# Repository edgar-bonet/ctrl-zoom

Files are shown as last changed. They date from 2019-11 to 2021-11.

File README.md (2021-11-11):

# LANC zoom controller

This project is a circuit board intended to control a DC motor from a
“zoom controller” wired remote conforming to the Sony's LANC protocol.

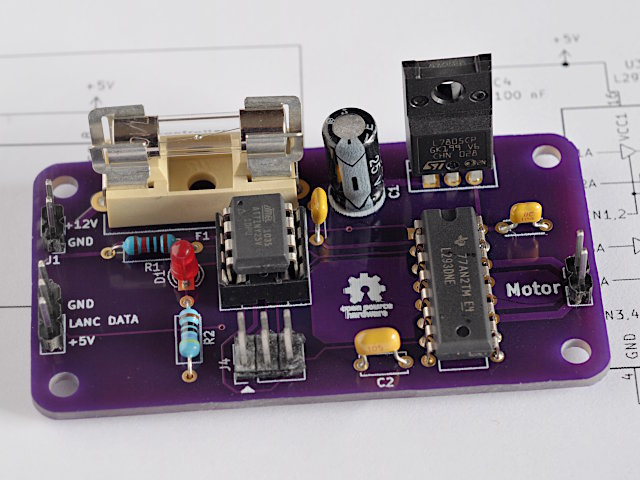
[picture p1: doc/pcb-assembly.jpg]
PCB assembly


## Motivation

Many people use DSLRs to record high-quality video despite their
inferior ergonomics relative to conventional camcorders. When mounted on
a tripod, many camcorders can be zoomed in and out using a wired remote
control, commonly known as a “[zoom controller][]”. In contrast, most
DSLRs have non-motorized zooms, and reaching for the zoom ring is
inconvenient when the camera is tripod-mounted.

The purpose of this project is to be able to control the zoom ring of a
DSLR using the same kind of wired remote one would use with a camcorder.
Specifically, this circuit board interfaces with remotes supporting the
widely used Sony's [LANC protocol][], and is capable of driving a
low-power DC motor from a 12&nbsp;V power supply. It is up to the user
to rig a DC motor to the zoom ring of their lens.

[zoom controller]: http://www.google.com/search?q=LANC+zoom+controller
[LANC protocol]: https://en.wikipedia.org/wiki/LANC

## Principle of operation

The main parts of the circuit are an [H bridge][] for driving the DC
motor and an [ATtiny][] microcontroller for driving the H bridge and
handling the communication with the wired remote.

The remote sends commands such as “zoom in at speed #2” or “zoom out at
speed #5”. In response to these commands, the microcontroller sets the
direction of rotation of the motor, and sends a [PWM][] signal to the
“enable” input of the H bridge. The duty cycle of the PWM signal depends
on the speed selected by the remote. This duty cycle in turn controls
the average power received by the DC motor. There is no feedback from
the motor, thus no precise control on its actual rotational speed.

[H bridge]: https://en.wikipedia.org/wiki/H_bridge
[ATtiny]: https://www.microchip.com/wwwproducts/en/ATtiny25
[PWM]: https://en.wikipedia.org/wiki/Pulse-width_modulation

## Building the circuit

Build the PCB according to the layout file
[ctrl-zoom.kicad\_pcb](board/ctrl-zoom.kicad_pcb), which is in the
format of the free [KiCad design software][KiCad]. Many professional PCB
shops can do it for you if you provide the proper design files. Some
accept the KiCad format directly, and need only that file. Others
require the design to be provided as a set of “Gerber” and drill files.
In this case, [install KiCad][KiCad-download], open ctrl-zoom.kicad\_pcb
with KiCad, and let it generate the required files (menu: File →
Plot...).

Get the parts listed below and solder them to the board. All are
through-hole components. Refer to the [schematic](doc/schematic.pdf) and
the labels on the PCB's silkscreen for the correct placement and
orientations.

| designator | quantity | item
|:---:|:---:|---
| U1 | 1 | L7805 voltage regulator, 5 V, TO-220 package
| U2 | 1 | ATtiny25-20PU, DIP-8 package [1]
| U3 | 1 | L293D H-bridge, DIP-16 package
| C1 | 1 | 100 µF radial electrolytic capacitor, ⌀ 6.3 mm
| C2 | 1 | 1 µF ceramic capacitor, pin spacing: 5 mm
| C3, C4 | 2 | 100 nF ceramic capacitor, pin spacing: 5 mm
| J1, J3 | 2 | 1×2 male pin header, pitch: 2.54 mm
| J2 | 1 | 1×3 male pin header, pitch: 2.54 mm
| J4 | 1 | 2×3 male pin header, pitch: 2.54 mm
| F1 | 1 | 1 A, 5×20 mm fuse + Stelvio-Kontek PTF78 holder
| D1 | 1 | 3 mm LED
| R1 | 1 | 10 kΩ resistor
| R2 | 1 | 470 Ω resistor

[1] Any ATtiny of the same family can be used (25, 25V, 45, 45V, 85, or
85V). It is recommended to use a DIP-8 socket, rather than soldering the
ATtiny directly to the board.

## Building and uploading the firmware

You need GNU make, avr-gcc, avr-libc, avrdude and an ISP programmer. An
Arduino [can be used as an ISP programmer][ArduinoISP]. On Ubuntu Linux,
you can install the required software by typing:

```shell
sudo apt install make gcc-avr avr-libc avrdude
```

Move to the firmware directory, edit the `MCU` and `PROGRAMMER`
variables in the Makefile, then type:

```shell
make
```

For uploading the firmware, connect the programmer to your computer and
the ISP header (J4) on the board, paying attention to the orientation
(pin 1 is bottom left, identified by the white triangle). Then type:

```shell
make upload
```

[KiCad]: https://www.kicad.org/
[KiCad-download]: https://www.kicad.org/download/
[ArduinoISP]: https://www.arduino.cc/en/Tutorial/ArduinoISP

## Usage

You will first have to rig a geared DC motor to the zoom ring of your
lens. Then connect the LANC wired remote to the connector on the left
side of the PCB labeled “J2” and the motor to the right-side connector
(J3). The power supply should be connected last, to J1. Actuate the
remote and check that the lens zooms in the desired direction. If this
is not the case, reverse the connection of the motor on J3.

If you are not pleased with the way the motor power varies as a function
of the remote's knob position, you can customize this dependency by
modifying the firmware. Near the top of
[ctrl-zoom.c](firmware/ctrl-zoom.c), locate the lines:

```c++
/* Available motor speeds. */
static __flash const uint8_t speeds[8] = {
    2, 4, 8, 16, 32, 64, 128, 255
};
```

These are the PWM levels corresponding to the 8 speeds that the remote
can request. Change these to your liking, rebuild the firmware and
upload it again (with the supply, the remote and the motor
disconnected).

## License

This project is [open-source hardware][OSH]. All of its files, including
firmware source code, design files and documentation, are provided under
the terms of the MIT licence. See the included [LICENSE](LICENSE) file.

If you use any of this, I would appreciate if you drop me a note. If you
improve on it, you are encouraged to contribute the changes back to the
open-hardware community. These are not, however, legal requirements:
only the terms of the license are legally binding.

[OSH]: https://en.wikipedia.org/wiki/Open-source_hardware

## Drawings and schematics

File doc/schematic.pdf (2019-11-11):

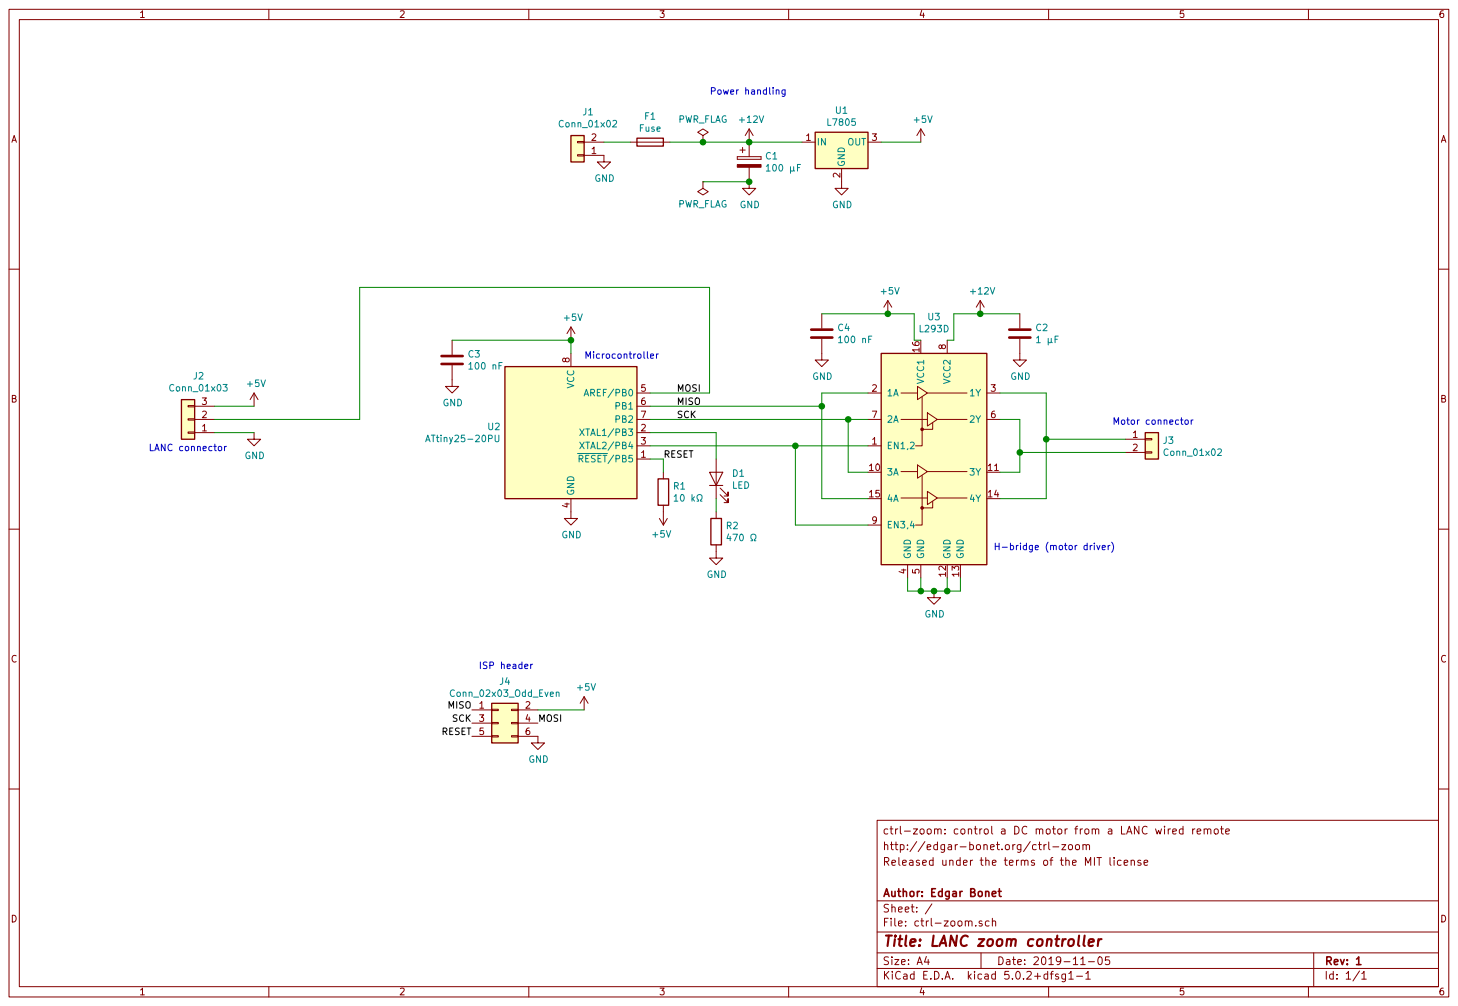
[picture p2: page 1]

http://edgar-bonet.org/ctrl-zoom
Id: 1/1 Title: LANC zoom controller File: ctrl-zoom.sch Sheet: / Author: Edgar Bonet Released under the terms of the MIT license

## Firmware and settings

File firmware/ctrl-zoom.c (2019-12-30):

/*
 * LANC receiver for ATtiny{2,4,8}5.
 * Based on:
 * Simple ATtiny USI UART <http://www.technoblogy.com/show?VSX>
 *
 * Pinout:
 *   5 = PB0 (DI)  LANC data
 *   6 = PB1       driver inputs 1 & 4
 *   7 = PB2       driver inputs 2 & 3
 *   3 = PB4       driver "enable" inputs
 *   2 = PB3       LED
 * Pin numbers are for the DIP8 package.
 *
 * Timer configuration:
 *  - TIM0_COMPB fires an interrupt at every bit transition, even when
 *    there is no transmission
 *  - TIM0_COMPA clocks the USI, the interrupt is not enabled
 * __        ____  ____  ____  ____  ____  ____  ____  ____  _______
 *   \      / D0 \/ D1 \/ D2 \/ D3 \/ D4 \/ D5 \/ D6 \/ D7 \/
 *    \____/\____/\____/\____/\____/\____/\____/\____/\____/
 *   B  A  B  A  B
 *
 * Timings:
 *   1 bit   =    104 us (9615 bps, i.e. 0.16% too fast)
 *   1 byte  =  1.248 ms = 12 bits (1 start, 8 data, 3 stop)
 *   1 frame = 19.968 ms = 16 bytes (4 rx-ed, 4 tx-ed, 8 skipped)
 */

#define F_CPU 8000000
#include <stdbool.h>
#include <avr/io.h>
#include <avr/interrupt.h>
#include <avr/sleep.h>
#include <util/delay.h>

#define PIN_DATA PB0
#define PIN_FW   PB1
#define PIN_REV  PB2
#define PIN_EN   PB4  /* OC1B */
#define PIN_LED  PB3

/* Available motor speeds. */
static __flash const uint8_t speeds[8] = {
    64, 78, 95, 116, 141, 172, 209, 255
};

uint8_t byte_cnt, bit_cnt;  /* byte and bit counters, could be fused */
volatile uint8_t recvd[2];    /* bytes received */
volatile bool data_received;  /* boolean */


/***********************************************************************
 * USI LANC driver.
 */

unsigned char reverse_byte(unsigned char x) {
    x = ((x >> 1) & 0x55) | ((x << 1) & 0xaa);
    x = ((x >> 2) & 0x33) | ((x << 2) & 0xcc);
    x = ((x >> 4) & 0x0f) | ((x << 4) & 0xf0);
    return x;
}

void init_usi_lanc(void) {
    DDRB   |= _BV(PIN_DATA);  /* define DI as output */
    TCCR0A  = _BV(WGM01);     /* timer in CTC mode */
    TCCR0B  = _BV(CS01);      /* prescaler to /8 */
    OCR0A   = 104 - 1;        /* shift every 104 us */
    OCR0B   = 104/2 - 1;      /* COMPB between successive COMPA */
    TIFR    = _BV(OCF0B);     /* clear output compare flag */
    TIMSK  |= _BV(OCIE0B);    /* enable output compare interrupt */
}

/* At every bit transition, even during the pause. */
ISR(TIM0_COMPB_vect)
{
    /* Are we in the pause? */
    if (byte_cnt & 8) goto done;

    /* Begin start bit. */
    if (bit_cnt == 0) {
        PORTB &= ~_BV(PIN_DATA);  /* floating */
        DDRB  |=  _BV(PIN_DATA);  /* output low */
    }

    /* End start bit. */
    else if (bit_cnt == 1) {

        /* Here we may want to transmit data instead... */
        DDRB  &= ~_BV(PIN_DATA);  /* floating */
        PORTB |=  _BV(PIN_DATA);  /* enable pullup */

        /* Start the USI receiver on bytes 0 and 1. */
        if (byte_cnt < 2) {
            USICR = _BV(USIOIE) | _BV(USICS0);
            USISR = _BV(USIOIF) | 8;
        }
    }

done:
    /* Increment (byte_cnt, bit_cnt) before returning. */
    if (++bit_cnt >= 12) {
        byte_cnt = (byte_cnt + 1) % 16;
        bit_cnt = 0;
    }
}

/* When a complete byte is received. */
ISR(USI_OVF_vect) {
    USICR = 0;                      /* Disable USI */
    recvd[byte_cnt] = ~reverse_byte(USIBR);
    if (byte_cnt == 1) data_received = true;
}


/***********************************************************************
 * Main program.
 */

/* Power the motor. */
static void control_motor()
{
    uint8_t output = 0;
    if (recvd[0] == 0x28) {  /* move */
        if (recvd[1] & 0x10)
            output = _BV(PIN_REV);  /* wide */
        else
            output = _BV(PIN_FW);  /* tele */
        output |= _BV(PIN_LED);
        OCR1B = speeds[recvd[1] >> 1 & 7];
    } else {
        OCR1B = 0;
    }
    PORTB = output;
}

int main(void)
{
    /* Set main clock prescaler to 1 => f_CPU = 8 MHz. */
    CLKPR = 1<<CLKPCE;
    CLKPR = 0;

    /* Configure Timer 1 for PWM on PIN_EN = PB4 = OC1B */
    GTCCR = _BV(PWM1B)    /* enable PWM on OC1B */
          | _BV(COM1B1);  /* non-inverting, nOC1B not connected */
    TCCR1 = _BV(CS11)     /* clock @ F_CPU/32 = 250 kZ -> ~ 1 kHz */
          | _BV(CS12);

    init_usi_lanc();
    sei();

    /* Configure outputs. */
    DDRB = _BV(PIN_FW)
         | _BV(PIN_REV)
         | _BV(PIN_EN)
         | _BV(PIN_LED);

    /* Main loop. */
    for (;;) {
        if (data_received) {
            control_motor();
            data_received = false;
        }
        sleep_mode();
    }
}

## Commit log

2019-12-30 Lower the PWM frequency
2021-11-09 Update README.md
    https://forum.kicad.info/t/warning-avoid-all-links-to-kicad-pcb-org-use-kicad-org/31521
2021-11-11 Doc: use the https URL for KiCad
    This prevents a redirect.
